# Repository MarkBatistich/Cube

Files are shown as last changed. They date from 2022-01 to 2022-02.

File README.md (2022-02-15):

# Cube

## Dynamic Model

To start, I drew a model of the sytem and defined some variables.

20220209_165314000_iOS

$\theta_w$ - angle of the wheel

$\theta_f$ - angle of the frame

$T$ - motor torque

$C_w$ - motor friction torque coefficient

$C_f$ - frame friction torque coefficient

$F_w$ - force of gravity on the wheel

$F_f$ - force of gravity on the frame

$I_c^o$ - moment of inertia of the cube about the origin

$I_w$ - moment of inertia of the wheel about its center of mass

$M_c^o$ - moment on the cube about the origin

$M_w$ - moment of the wheel about its center of mass

$m_w$ - mass of the wheel

$m_f$ - mass of the frame

$m_c$ - mass of the cube

$l_w$ - distance between the wheel's center of mass and the origin

$l_f$ - distance between the frame's center of mass and the origin

$l_c$ - distance between the cube's center of mass and the origin

I also defined the intertial axis such that +x is parellel to an unsloped surface and parallel to the cube face, +y is normal to an unsloped surface in the opposite direction as the force of gravity, and +z is in the direction of counterclockwise (CCW) wheel rotation. The origin O is placed at the corner of the cube touching the surface.

The equations of motion are constructed from the moments.

$M_c^o = I_c^o\ddot{\theta}_f = m_cl_cgsin(\theta_f) - (T - C_w\dot{\theta_w})-C_f\dot{\theta}_f$

$M_w = I_w(\ddot{\theta}_f+\ddot{\theta}_w) = T-C_w\dot{\theta_w}$

The cube moment of inertia about the origin can be found from the parallel axis theorem.

$I_c^o = I_f^o + I_w^o = I_f+m_fl_f^2 + I_w+m_wl_w^2$

The moment equations are solved for angular acceleration

$\ddot{\theta}_f = \frac{m_cl_cgsin(\theta_f)-T+C_w\dot{\theta_w}-C_f\dot{\theta}_f}{I_c^o}$

$\ddot{\theta}_w = \frac{T- C_w\dot{\theta_w}}{I_w} - \ddot{\theta}f$

From these equations, a state space model is made:

$x_1=\theta_f, x_2=\dot{\theta}_f,x_3=\dot{\theta}_w$

$\dot{x}_1 = x_2$

$\dot{x}_2 = \frac{m_cl_cgsin(\theta_f)-T+C_w\dot{\theta_w}-C_f\dot{\theta}_f}{I_c^o}$

$\dot{x}_3 = \frac{T- C_w\dot{\theta_w}}{I_w} - \frac{m_cl_cgsin(\theta_f)-T+C_w\dot{\theta_w}-C_f\dot{\theta}_f}{I_c^o}$

The small angle approximation is applied: $\sin(\dot{\theta}_f)=\dot{\theta}_f$

The torque is related to the pwm input $u$ by the equation:

$T = K_tu$

where $K_t$ is the motor torque constant.

The state space equations are put into matrix form:

$\begin{bmatrix}
\dot{x}_1 \\
\dot{x}_2 \\
\dot{x}_3 
\end{bmatrix} = 
\begin{bmatrix}
0 & 1 & 0\\
\frac{m_cl_cg}{I_c^o} & -\frac{C_f}{I_c^o} & \frac{C_w}{I_c^o}\\
-\frac{m_cl_cg}{I_c^o} & \frac{C_f}{I_c^o} & -\frac{C_w}{I_w}-\frac{C_w}{I_c^o}
\end{bmatrix}
\begin{bmatrix}
x_1 \\
x_2 \\
x_3 
\end{bmatrix} + 
\begin{bmatrix}
0 \\
-\frac{K_t}{I_c^o} \\
\frac{K_t}{I_w}-\frac{K_t}{I_c^o}
\end{bmatrix} u $

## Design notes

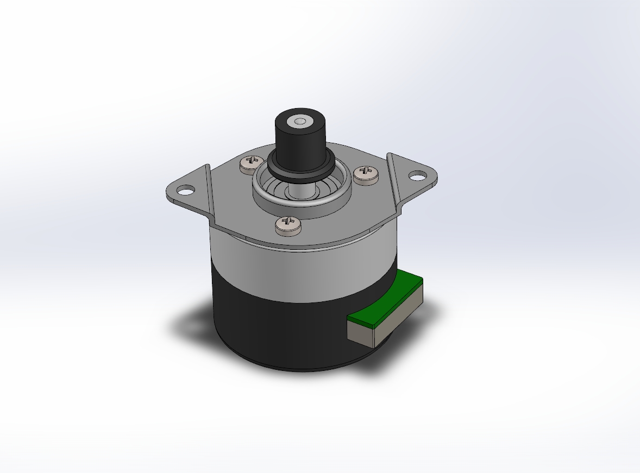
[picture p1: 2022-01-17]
CAD/c.jpg

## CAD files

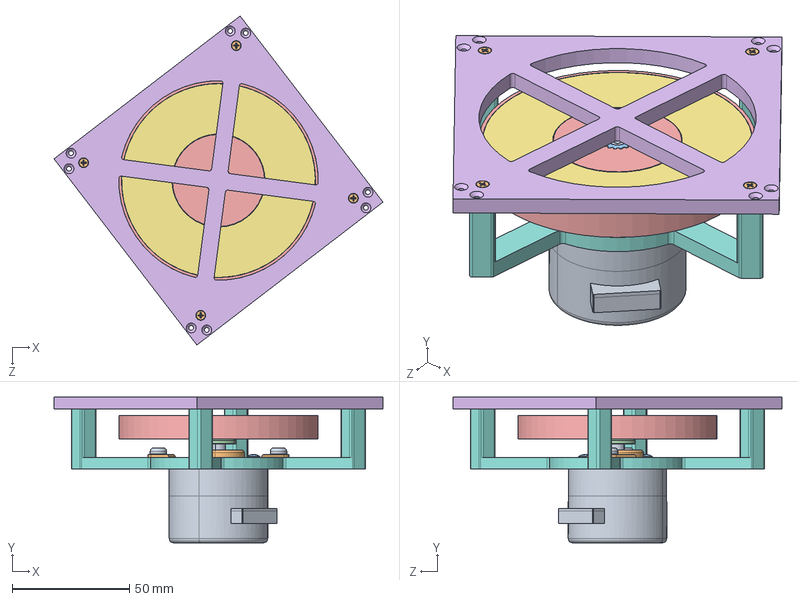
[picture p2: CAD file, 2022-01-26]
CAD/MotorAssembly.SLDASM
140.2 x 62.0 x 140.2 mm
motor.STEP
mount_plate.STEP
pan head cross recess screw_iso_ISO 7045 - M3 x 4 - Z - 4N.STEP x 3
pulley_nidec.STEP
Wheel
WheelCover
92141A041_18-8 Stainless Steel Washer x 2
MotorHolder2
99461A963_Phillips Rounded Head Thread-Forming Screws x 2
90485A416_Stainless Steel Flat Head Thread-Forming Screws for Plastic x 4
Geare

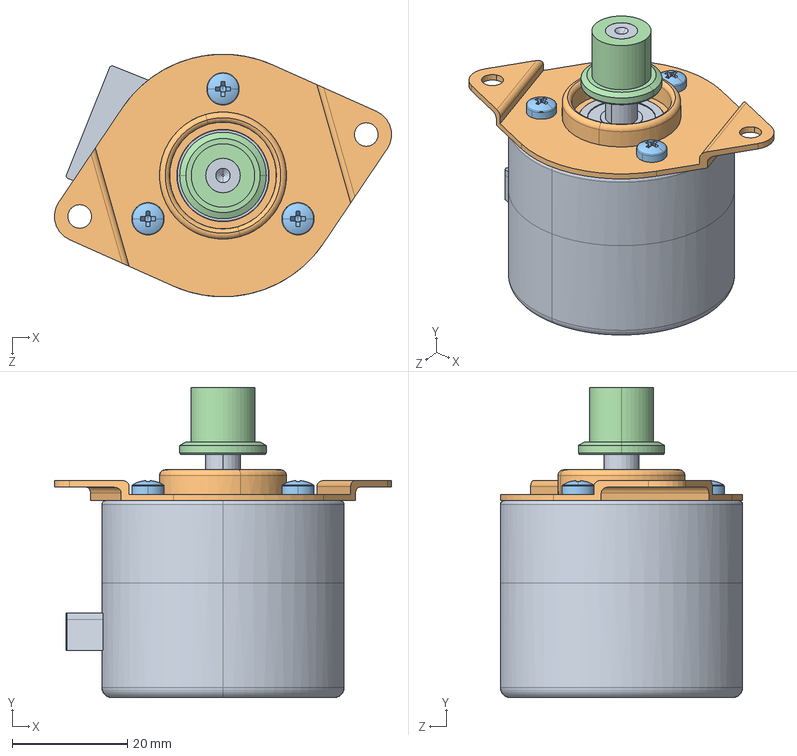
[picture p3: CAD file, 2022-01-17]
CAD/Motor.SLDASM
58.4 x 53.8 x 42.0 mm
motor.STEP
mount_plate.STEP
pan head cross recess screw_iso_ISO 7045 - M3 x 4 - Z - 4N.STEP x 3
pulley_nidec.STEP

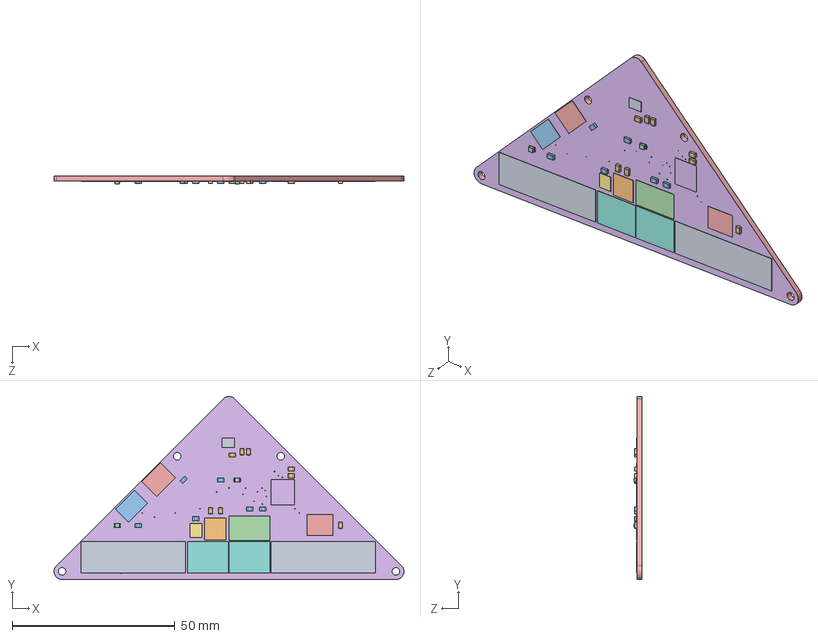
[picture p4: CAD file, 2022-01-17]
CAD/pcb v8.step.SLDASM
107.5 x 56.3 x 2.50 mm
PQFN50P300X250X97-14N.step
AP220533YR13.step
CUS-12B.step
OS102011MS2QS1.step
PTS526SM15SMTR2LFS.step x 2
SOP65P640X120-20N.step
SOT95P285X140-3N.step
TB00250002BE.step x 2
TB00250006BE.step x 2
C0805.step x 8
R0805.step x 6
CHIP-LED0805.step x 2
Board.step
1-soldermask.step
16-soldermask.step

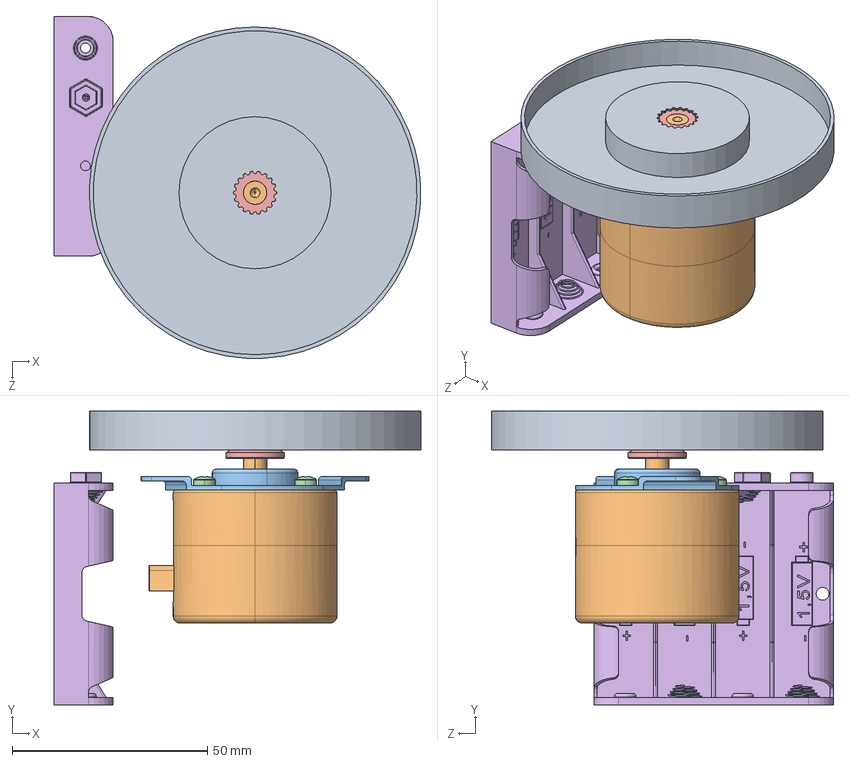
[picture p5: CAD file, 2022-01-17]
CAD/Assem.SLDASM
94.0 x 75.3 x 87.7 mm
Wheel
motor.STEP
mount_plate.STEP
pan head cross recess screw_iso_ISO 7045 - M3 x 4 - Z - 4N.STEP x 3
pulley_nidec.STEP
Battery2

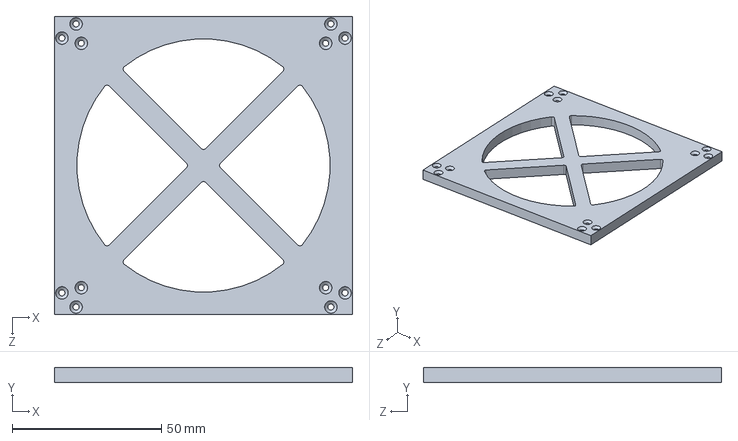
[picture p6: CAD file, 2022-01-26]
CAD/WheelCover.SLDPRT
100.0 x 5.00 x 100.0 mm

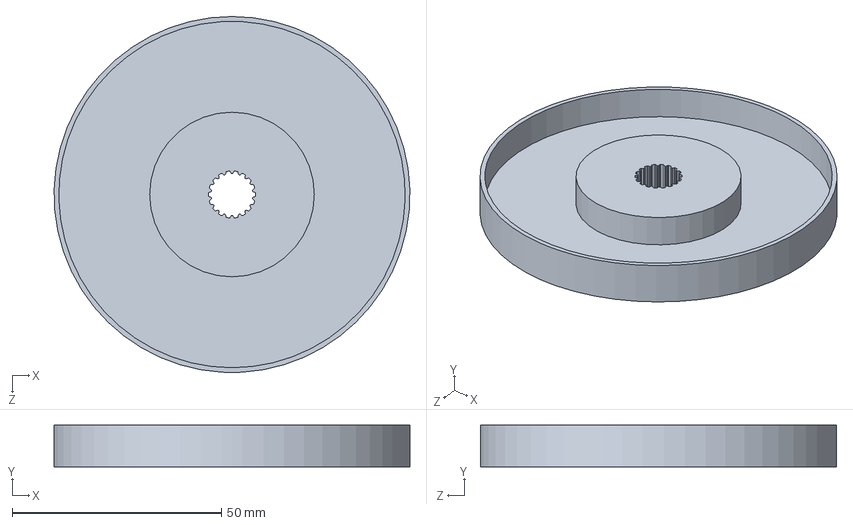
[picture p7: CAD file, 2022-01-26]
CAD/Wheel.SLDPRT
85.0 x 10.0 x 85.0 mm

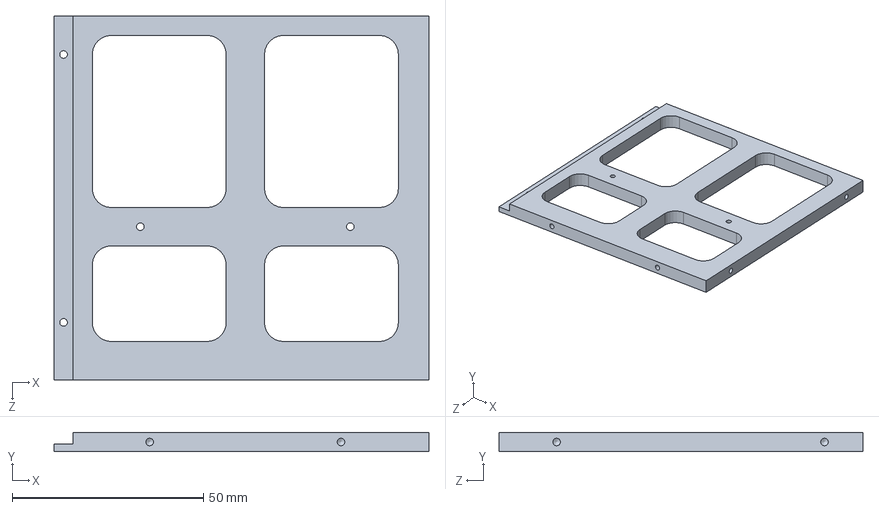
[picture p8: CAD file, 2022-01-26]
CAD/Wall.SLDPRT
98.0 x 5.00 x 95.0 mm

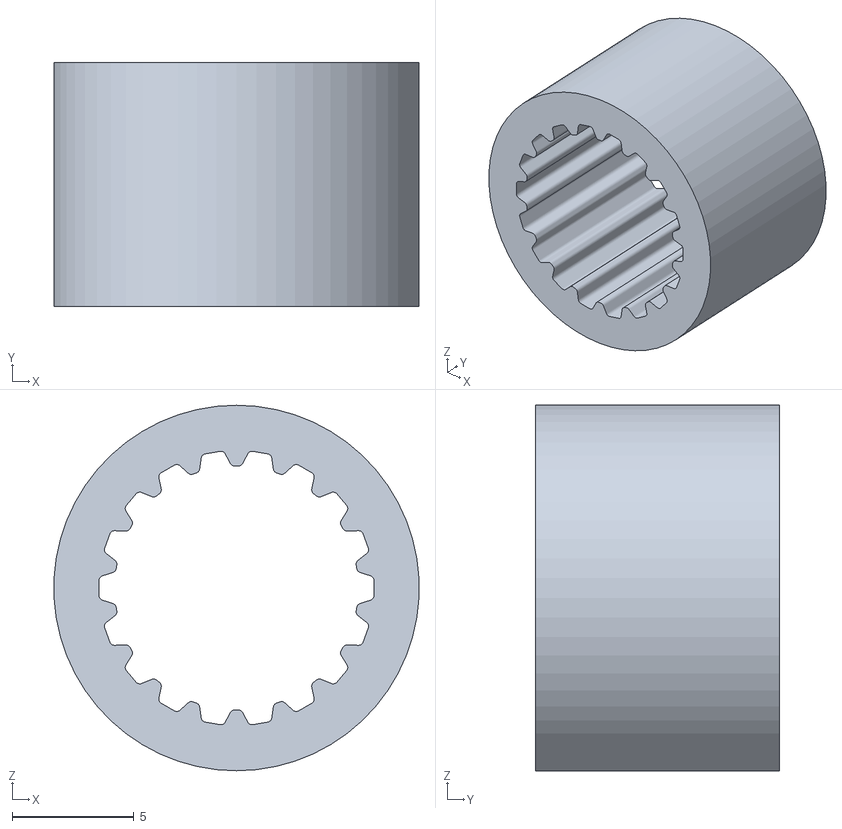
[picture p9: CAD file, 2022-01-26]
CAD/GearTest.STL
15.0 x 10.0 x 15.0

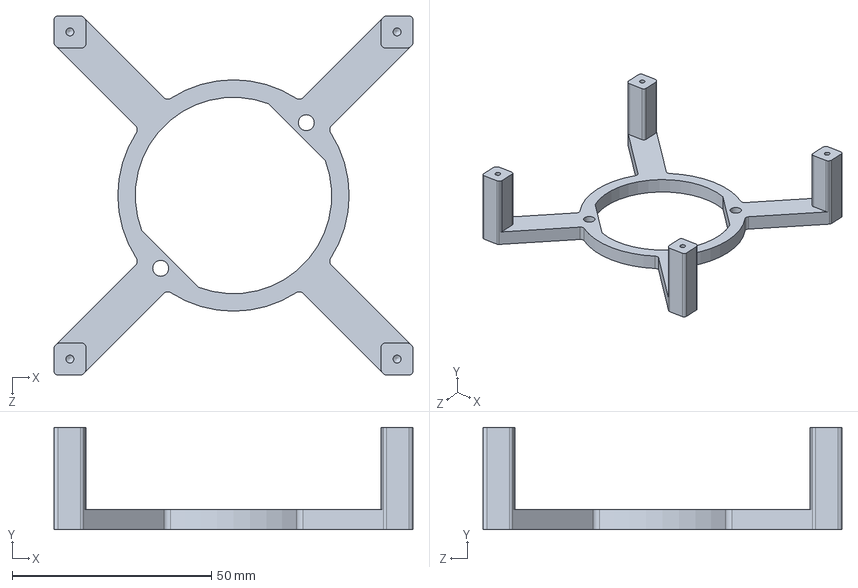
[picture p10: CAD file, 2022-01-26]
CAD/MotorHolder2.SLDPRT
90.0 x 25.6 x 90.0 mm

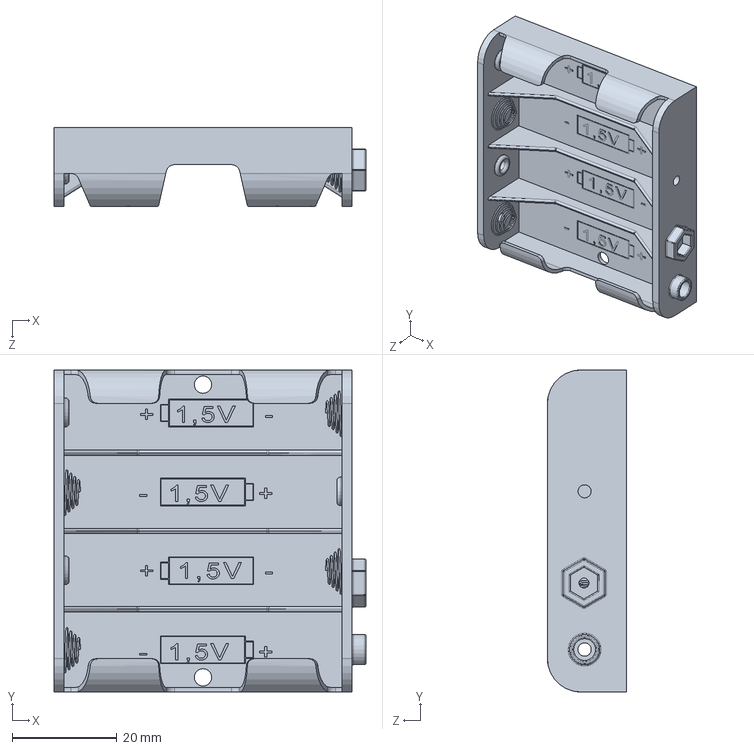
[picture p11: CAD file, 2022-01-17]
CAD/Battery2.SLDPRT
59.6 x 61.5 x 15.1 mm

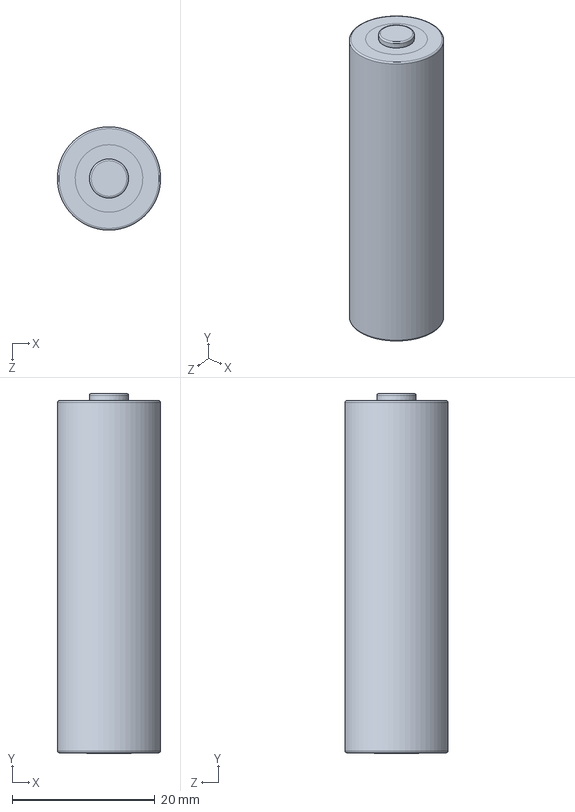
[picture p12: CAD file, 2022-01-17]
CAD/AA Battery.SLDPRT
14.5 x 50.5 x 14.5 mm

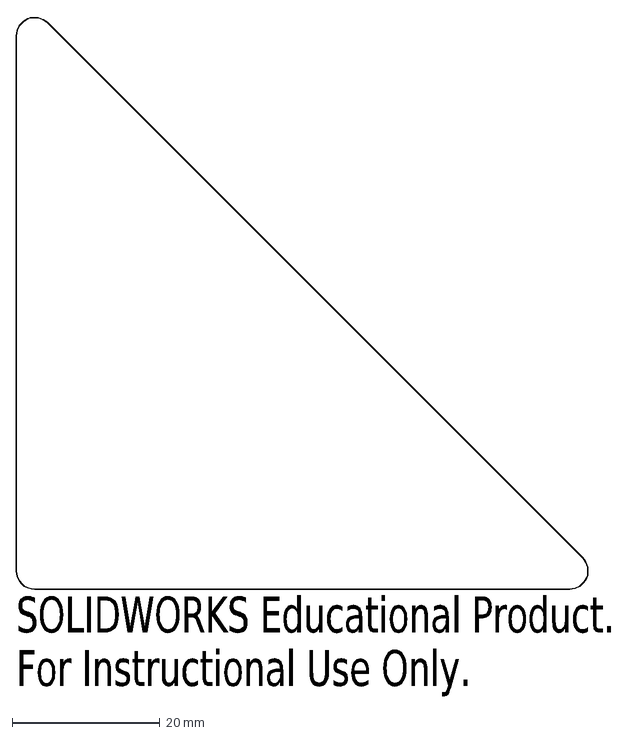
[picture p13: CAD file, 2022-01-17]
CAD/PCBshape1.DXF
SOLIDWORKS Educational Product.
For Instructional Use Only.

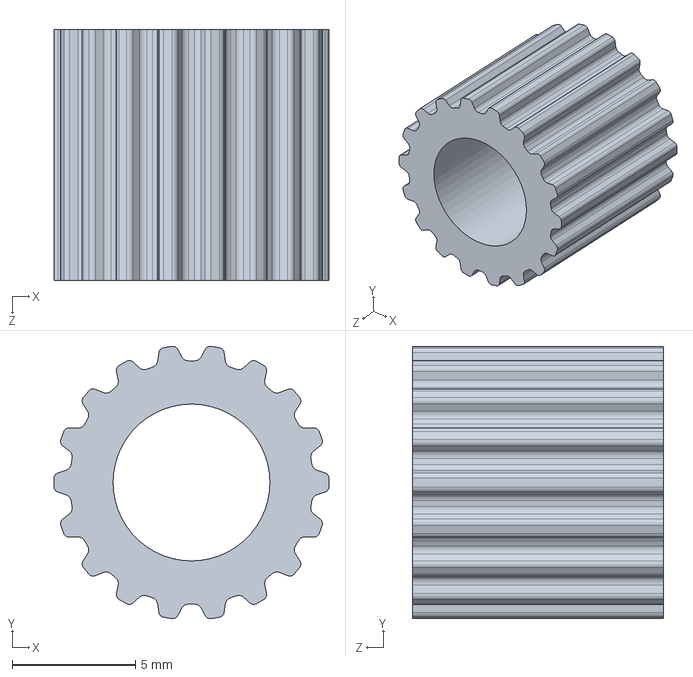
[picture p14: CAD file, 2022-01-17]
CAD/Geare.SLDPRT
11.1 x 11.0 x 10.2 mm

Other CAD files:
CAD/Packages.step.SLDASM
CAD/CHIP-LED0805.step.SLDPRT
CAD/Assem1.STEP
CAD/PTS526SM15SMTR2LFS.step.SLDPRT
CAD/pcb v8-2.step
CAD/1-copper.step.SLDPRT
CAD/1-soldermask.step.SLDPRT
CAD/16-soldermask.step.SLDPRT
CAD/7712K14_Battery Holder.SLDPRT
CAD/90107A042_316 Stainless Steel Washer.SLDPRT
CAD/90485A416_Stainless Steel Flat Head Thread-Forming Screws for Plastic.SLDPRT
CAD/92141A041_18-8 Stainless Steel Washer.SLDPRT
CAD/99461A922_Phillips Rounded Head Thread-Forming Screws.SLDPRT
CAD/99461A963_Phillips Rounded Head Thread-Forming Screws.SLDPRT
CAD/AP220533YR13.step.SLDPRT
CAD/Assem1.IGS
CAD/Assem1.STL
CAD/Assem1.x_b
CAD/Battery.SLDPRT
CAD/Board.step.SLDPRT
CAD/BoardShapeTest.SLDPRT
CAD/C0805.step.SLDPRT
CAD/CUS-12B.step.SLDPRT
CAD/MotorHolder.SLDPRT
CAD/MotorHolder2.STL
CAD/OS102011MS2QS1.step.SLDPRT
CAD/PQFN50P300X250X97-14N.step.SLDPRT
CAD/R0805.step.SLDPRT
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

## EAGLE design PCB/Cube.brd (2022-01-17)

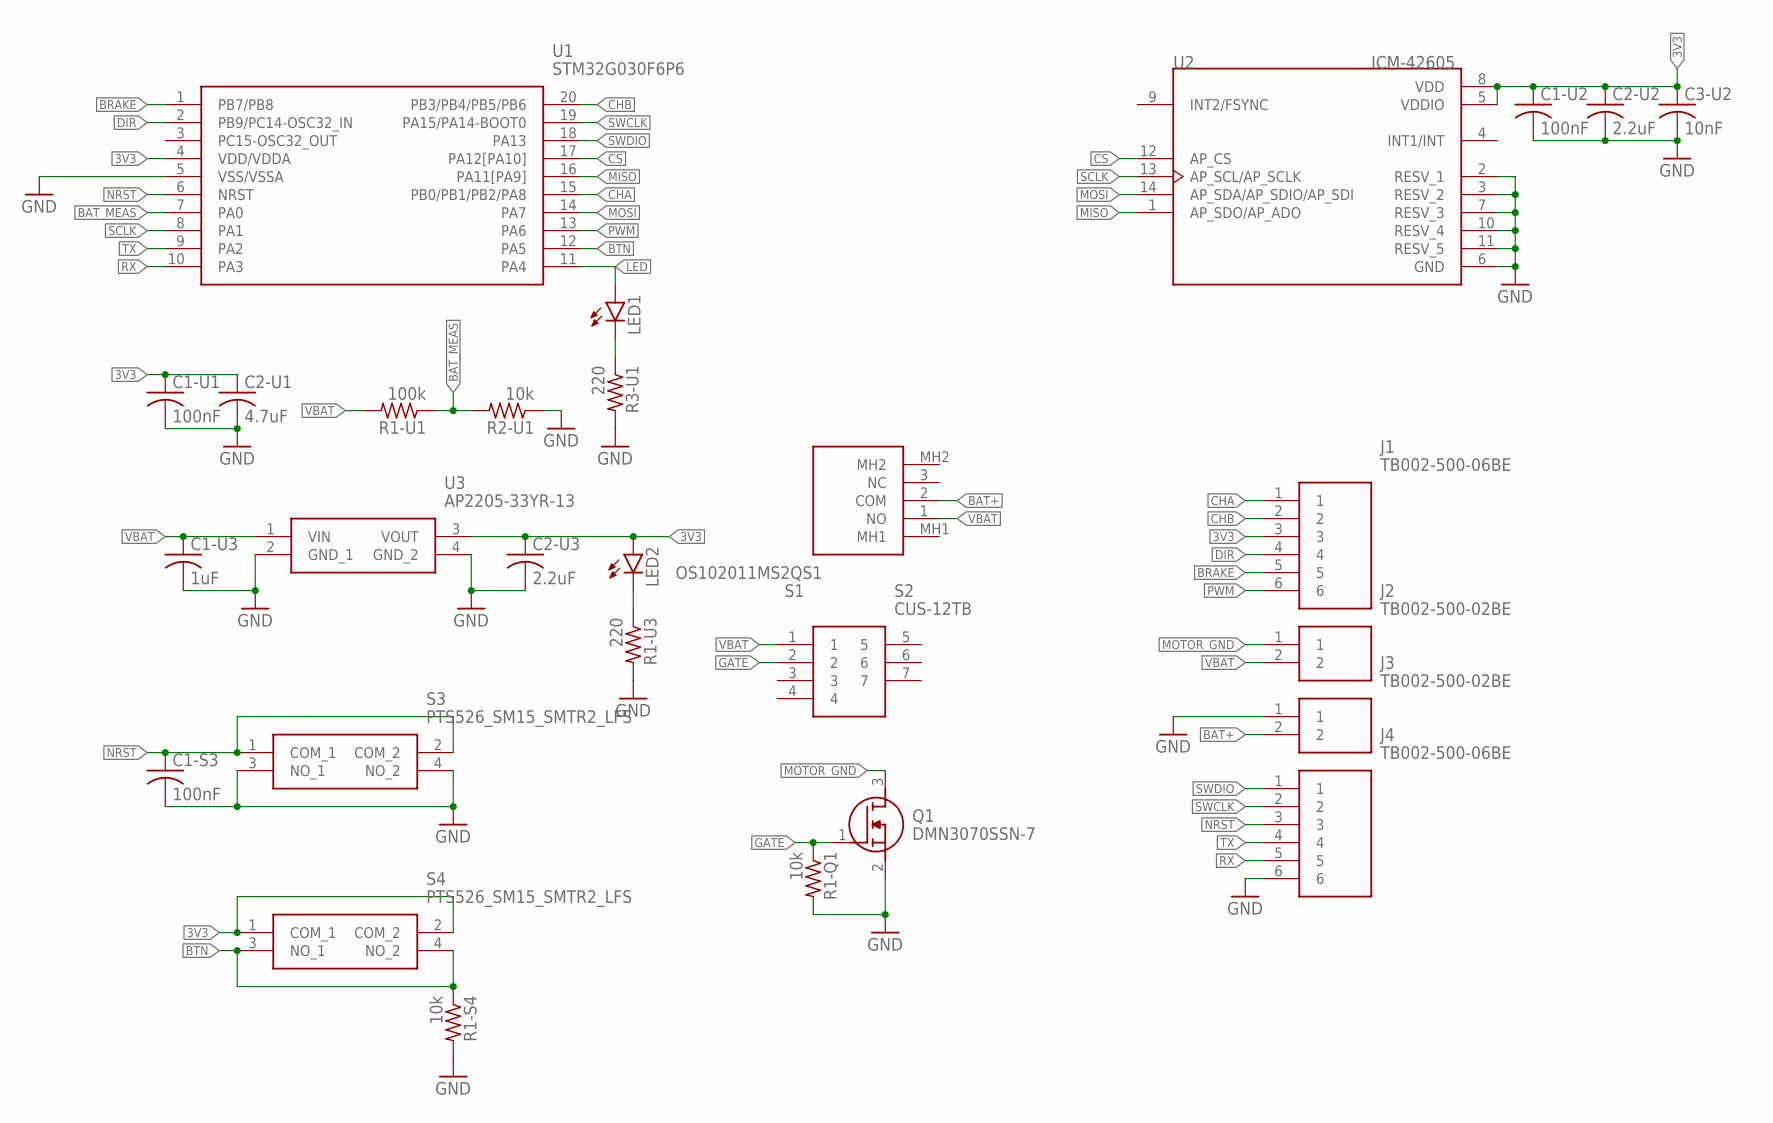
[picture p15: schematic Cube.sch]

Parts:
C1-S3, C1-U1, C1-U2: 100nF; C0805
C1-U3: 1uF; C0805
C2-U1: 4.7uF; C0805
C2-U2, C2-U3: 2.2uF; C0805
C3-U2: 10nF; C0805
J1, J4: TB002-500-06BE; TB00250006BE
J2, J3: TB002-500-02BE; TB00250002BE
LED1, LED2: LEDCHIP-LED0805; CHIP-LED0805
Q1: DMN3070SSN-7; SOT95P285X140-3N
R1-Q1, R1-S4, R2-U1: 10k; R0805
R1-U1: 100k; R0805
R1-U3, R3-U1: 220; R0805
S1: OS102011MS2QS1
S2: CUS-12TB; CUS-12B
S3, S4: PTS526_SM15_SMTR2_LFS; PTS526SM15SMTR2LFS
U1: STM32G030F6P6; SOP65P640X120-20N
U2: ICM-42605; PQFN50P300X250X97-14N
U3: AP2205-33YR-13; AP220533YR13

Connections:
3V3: C1-U1.1, C1-U2.1, C2-U1.1, C2-U2.1, C2-U3.1, C3-U2.1, J1.3, LED2.A, S4.1 (COM_1), S4.2 (COM_2), U1.4 (VDD/VDDA), U2.5 (VDDIO), U2.8 (VDD), U3.3 (VOUT)
BAT+: J3.2, S1.2 (COM)
BAT_MEAS: R1-U1.1, R2-U1.2, U1.7 (PA0)
BRAKE: J1.5, U1.1 (PB7/PB8)
BTN: R1-S4.1, S4.3 (NO_1), S4.4 (NO_2), U1.12 (PA5)
CHA: J1.1, U1.15 (PB0/PB1/PB2/PA8)
CHB: J1.2, U1.20 (PB3/PB4/PB5/PB6)
CS: U1.17 (PA12[PA10]), U2.12 (AP_CS)
DIR: J1.4, U1.2 (PB9/PC14-OSC32_IN)
GATE: Q1.1 (G), R1-Q1.1, S2.2
GND: C1-S3.2, C1-U1.2, C1-U2.2, C1-U3.2, C2-U1.2, C2-U2.2, C2-U3.2, C3-U2.2, J3.1, J4.6, Q1.2 (S), R1-Q1.2, R1-S4.2, R1-U3.2, R2-U1.1, R3-U1.2, S3.3 (NO_1), S3.4 (NO_2), U1.5 (VSS/VSSA), U2.2 (RESV_1), U2.3 (RESV_2), U2.6 (GND), U2.7 (RESV_3), U2.10 (RESV_4), U2.11 (RESV_5), U3.2 (GND_1), U3.4 (GND_2)
LED: LED1.A, U1.11 (PA4)
LED1-R: LED1.C, R3-U1.1
LED2-R: LED2.C, R1-U3.1
MISO: U1.16 (PA11[PA9]), U2.1 (AP_SDO/AP_ADO)
MOSI: U1.14 (PA7), U2.14 (AP_SDA/AP_SDIO/AP_SDI)
MOTOR_GND: J2.1, Q1.3 (D)
NRST: C1-S3.1, J4.3, S3.1 (COM_1), S3.2 (COM_2), U1.6 (NRST)
PWM: J1.6, U1.13 (PA6)
RX: J4.5, U1.10 (PA3)
SCLK: U1.8 (PA1), U2.13 (AP_SCL/AP_SCLK)
SWCLK: J4.2, U1.19 (PA15/PA14-BOOT0)
SWDIO: J4.1, U1.18 (PA13)
TX: J4.4, U1.9 (PA2)
VBAT: C1-U3.1, J2.2, R1-U1.2, S1.1 (NO), S2.1, U3.1 (VIN)

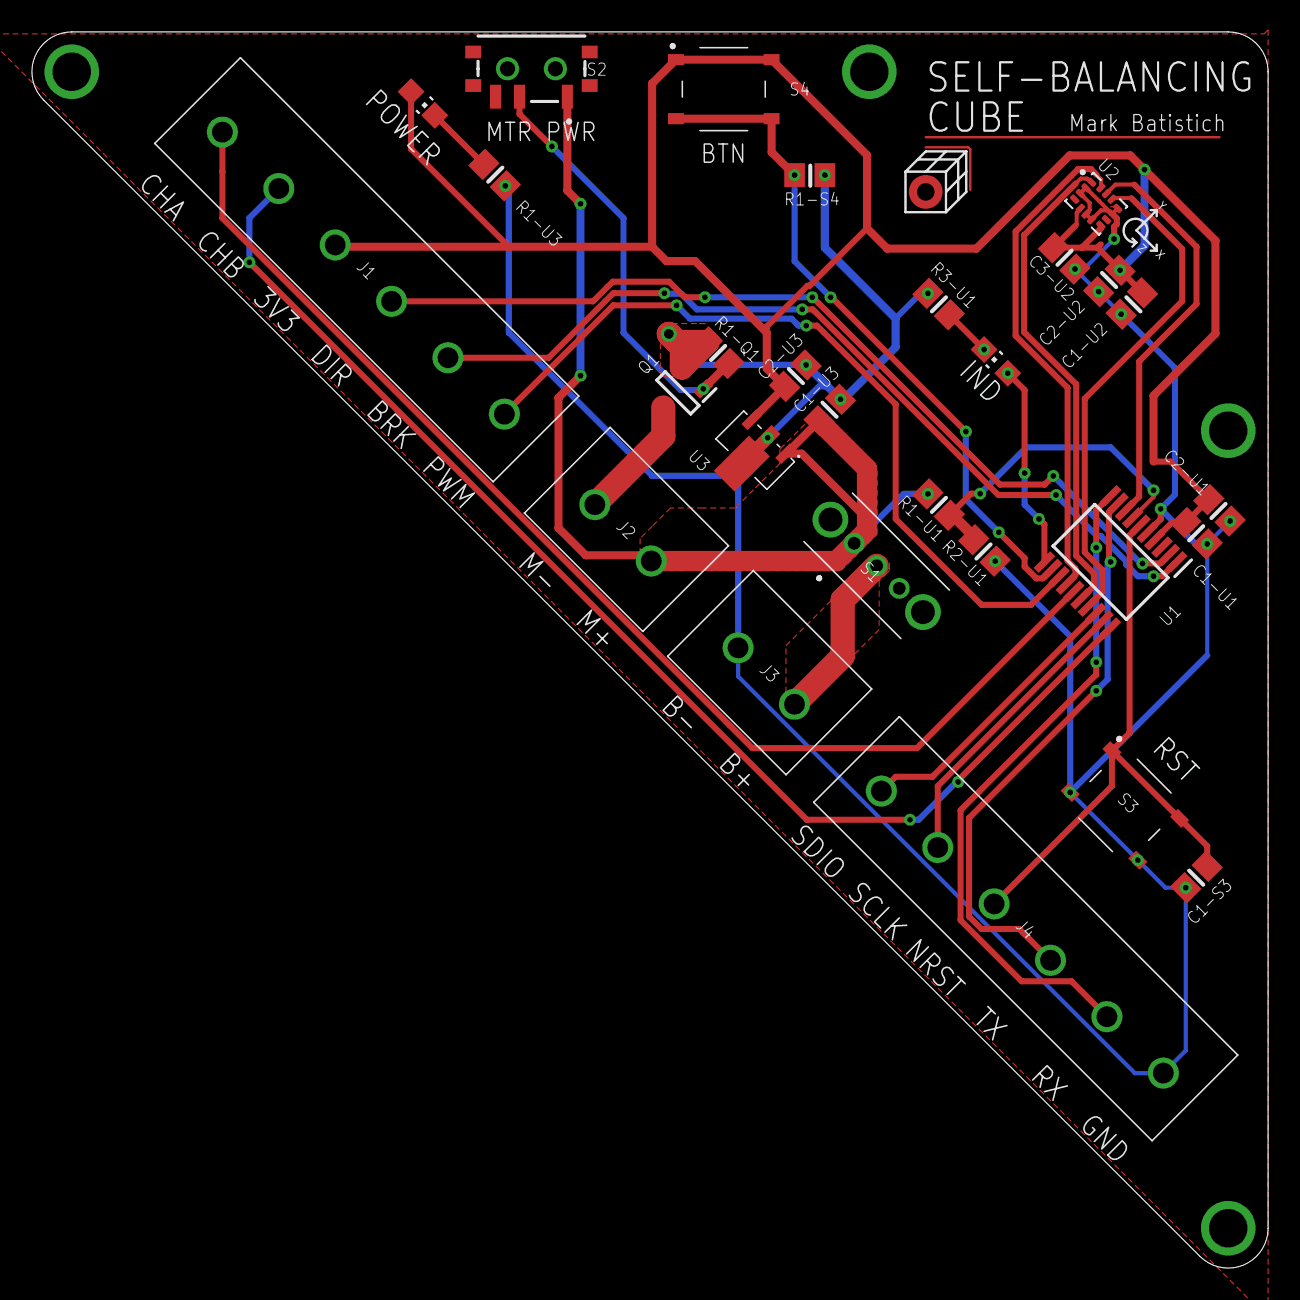
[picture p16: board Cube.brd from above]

Board: 2 copper layers, 77.5 x 77.5 mm, 28 parts (0 on the bottom side), 25 nets.

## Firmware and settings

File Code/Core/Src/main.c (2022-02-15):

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
/* Includes ------------------------------------------------------------------*/
#include "main.h"

/* USER CODE BEGIN Includes */
#include <stdio.h>
#include "fixmath.h"
//#include <math.h>
/* USER CODE END Includes */

ADC_HandleTypeDef hadc1;

SPI_HandleTypeDef hspi1;

TIM_HandleTypeDef htim1;
TIM_HandleTypeDef htim3;

UART_HandleTypeDef huart2;

void SystemClock_Config(void);
static void MX_GPIO_Init(void);
static void MX_TIM1_Init(void);
static void MX_TIM3_Init(void);
static void MX_USART2_UART_Init(void);
static void MX_ADC1_Init(void);
static void MX_SPI1_Init(void);
/* USER CODE BEGIN 0 */
int _write(int file, char *ptr, int len)
{
	HAL_UART_Transmit(&huart2, (uint8_t*)ptr, len, HAL_MAX_DELAY);
	return len;
}

void resetICM()
{
	uint8_t tx[2] = {W | DEVICE_CONFIG, 0x01};
	HAL_GPIO_WritePin (CS_GPIO_Port, CS_Pin, GPIO_PIN_RESET);
	HAL_SPI_Transmit(&hspi1, tx, 2, 1000);
	HAL_GPIO_WritePin (CS_GPIO_Port, CS_Pin, GPIO_PIN_SET);
	HAL_Delay(1);
}

void spiSet(uint8_t addr, uint8_t val)
{
	uint8_t tx[2] = {0};
	tx[0] = W | addr;
	tx[1] = val;
	HAL_GPIO_WritePin (CS_GPIO_Port, CS_Pin, GPIO_PIN_RESET);
	HAL_SPI_Transmit(&hspi1, tx, 2, SPI_WAIT);
	HAL_GPIO_WritePin (CS_GPIO_Port, CS_Pin, GPIO_PIN_SET);
}

void spiGet(uint8_t addr, uint8_t* rx, uint8_t num)
{
	uint8_t tx = R | addr;
	HAL_GPIO_WritePin (CS_GPIO_Port, CS_Pin, GPIO_PIN_RESET);
	HAL_SPI_Transmit(&hspi1, &tx, 1, SPI_WAIT);
	HAL_SPI_Receive(&hspi1, rx, num, SPI_WAIT);
	HAL_GPIO_WritePin (CS_GPIO_Port, CS_Pin, GPIO_PIN_SET);
}

void printf16(fix16_t num, int decimals){
	decimals = decimals > 5 ? 5 : decimals;
	char str[14] = {'0'};
	fix16_to_str(num, str, decimals);
	printf("%s", str);
}

void pn(){
	printf("\r\n");
}

void ps(){
	printf(" ");
}

void pc(){
	printf(", ");
}

void brakeOn() {
	HAL_GPIO_WritePin(BRAKE_GPIO_Port, BRAKE_Pin, GPIO_PIN_RESET);
	return;
}

void brakeOff() {
	HAL_GPIO_WritePin(BRAKE_GPIO_Port, BRAKE_Pin, GPIO_PIN_SET);
	return;
}

void waitUntilStop(){
	TIM3->CCR1 = 100;
	brakeOn();
	int val1 = 0;
	int val2 = 1;
	while (val1 != val2){
		val1 = TIM1->CNT;
		HAL_Delay (10);
		val2 = TIM1->CNT;
	}
	brakeOff();
}

fix16_t getBatteryVoltage() {
	HAL_ADC_Start(&hadc1);
	uint32_t raw;
	fix16_t voltage;
	HAL_ADC_PollForConversion(&hadc1, 1000);
	raw = HAL_ADC_GetValue(&hadc1);
	voltage = fix16_mul(fix16_from_int(raw), fix16_from_float(3.3/4095*0.9647)); // Vdd / 2^16 * fudgeFactor
	voltage = fix16_mul(voltage, fix16_from_float(11.07)); // resistor ratio
	voltage = fix16_sub(voltage, fix16_from_float(0.1)); // more fudge factor
	HAL_ADC_Stop(&hadc1);
	return voltage;
}

fix16_t rad2deg(fix16_t num){
	num = fix16_mul(num, fix16_from_int(180));
	num = fix16_div(num, fix16_pi);
	return num;
}

//returns 1 if the number is negative, 0 if positive or 0
int32_t sign(int32_t num){
	return (num < 0);
}
/* USER CODE END 0 */

/**
  * @brief  The application entry point.
  * @retval int
  */
int main(void)
{
  /* MCU Configuration--------------------------------------------------------*/

  /* Reset of all peripherals, Initializes the Flash interface and the Systick. */
  HAL_Init();

  /* Configure the system clock */
  SystemClock_Config();

  /* Initialize all configured peripherals */
  MX_GPIO_Init();
  MX_TIM1_Init();
  MX_TIM3_Init();
  MX_USART2_UART_Init();
  MX_ADC1_Init();
  MX_SPI1_Init();
  /* USER CODE BEGIN 2 */

  //Start timers and ADC
  HAL_TIM_PWM_Start(&htim3, TIM_CHANNEL_1);
  HAL_TIM_Encoder_Start(&htim1, TIM_CHANNEL_ALL);

  uint8_t rx[6] = { 0 };
  resetICM();
  spiSet(ACCEL_CONFIG0, 0x06);
  spiSet(GYRO_CONFIG0, 0x06);
  spiSet(PWR_MGMT0, 0x0F);
  HAL_Delay(45);

//  fix16_t P = fix16_from_float(32767.999985);
//  fix16_t Q = fix16_atan2(140351, 65536);
//  P = fix16_div(P,Q);
//  Q = fix16_mul(Q, fix16_from_int(2));
//  P = fix16_sqrt(P);

  printf("start\r\n");
  pn();


  //variable definitions
  int16_t pos1 = 0, pos2 = 0, diff = 0;
  fix16_t angle = 0, prevAngle = 0, gyrAngle = 0, accAngle = 0;
  uint32_t start = 0, end = 0;
  uint8_t dir = 1;
  uint32_t pulse = TIM3->CCR1;
  int32_t control = 0, controlSignal = 0;
  int16_t a_i[3] = {0};
  fix16_t a_f[3] = {0};
  int16_t g_i[3] = {0};
  fix16_t g_f[3] = {0};
  fix16_t error = 0, errorInt = 0, errorDiff = 0;
  fix16_t velocity = 0;
  fix16_t controlVelocity = 0;
  fix16_t velocityError = 0, velocityErrorInt = 0, velocityErrorDiff = 0;
  fix16_t prevVelocityError = 0;
  uint8_t firstRun = 1;
  fix16_t angleControl, velocityControl = 0;


  const uint32_t dt = 10;
  const fix16_t tau = fix16_from_int(1);
  const fix16_t alpha = fix16_div(tau, fix16_add(tau, fix16_div(fix16_from_int(dt), fix16_from_int(1000))));
  const fix16_t accFactor = fix16_div(fix16_from_int(16), fix16_from_int(32768));
  const fix16_t gyrFactor = fix16_div(fix16_from_int(2000), fix16_from_int(32768));
  const fix16_t Kp = fix16_from_float(80.00);
  const fix16_t Ki = fix16_from_float(3.000);
  const fix16_t Kd = fix16_from_float(200.00);
  const fix16_t Kp_s = fix16_from_float(10.00);
  const fix16_t Ki_s = fix16_from_float(0.00);
  const fix16_t Kd_s = fix16_from_float(0.00);

  HAL_GPIO_WritePin(DIR_GPIO_Port, DIR_Pin, GPIO_PIN_RESET);
  HAL_GPIO_WritePin(LED_GPIO_Port, LED_Pin, GPIO_PIN_RESET);
  HAL_GPIO_WritePin(DIR_GPIO_Port, DIR_Pin, GPIO_PIN_SET);
  waitUntilStop();
  TIM3->CCR1 = 100;

  spiGet(WHO_AM_I, rx, 1);
  printf("WHO_AM_I: %d\r\n", rx[0]);
  HAL_Delay(1000);
  /* USER CODE END 2 */

  /* Infinite loop */
  /* USER CODE BEGIN WHILE */
  while (1)
  {
    /* USER CODE END WHILE */

    /* USER CODE BEGIN 3 */
	  start = HAL_GetTick();

	  pos1 = pos2;
	  pos2 = TIM1 -> CNT;
	  diff = pos2 - pos1;
	  if (diff < 0) diff += 65536;

	  spiGet(ACCEL_DATA_X1, rx, 6);

	  a_i[0] = (rx[0] << 8) | rx[1];
	  a_i[1] = (rx[2] << 8) | rx[3];
	  a_i[2] = (rx[4] << 8) | rx[5];

	  a_f[0] = fix16_mul(fix16_from_int(a_i[0]), accFactor);
	  a_f[1] = fix16_mul(fix16_from_int(a_i[1]), accFactor);
	  a_f[2] = fix16_mul(fix16_from_int(a_i[2]), accFactor);

	  spiGet(GYRO_DATA_X1, rx, 6);

	  g_i[0] = (rx[0] << 8) | rx[1];
	  g_i[1] = (rx[2] << 8) | rx[3];
	  g_i[2] = (rx[4] << 8) | rx[5];

	  g_f[0] = fix16_mul(fix16_from_int(g_i[0]), gyrFactor);
	  g_f[1] = fix16_mul(fix16_from_int(g_i[1]), gyrFactor);
	  g_f[2] = fix16_mul(fix16_from_int(g_i[2]), gyrFactor);

	  prevAngle = angle;
	  accAngle = fix16_atan2(-a_f[0], -a_f[1]);
	  accAngle = rad2deg(accAngle);
	  accAngle = fix16_sub(accAngle, fix16_from_float(1.5));

	  if (firstRun){
		  gyrAngle = accAngle;
		  angle = accAngle;
	  }

	  gyrAngle = fix16_add(angle, fix16_mul(-g_f[2], fix16_div(fix16_from_int(dt), fix16_from_int(1000))));

	  angle = fix16_add(fix16_mul(alpha, gyrAngle), fix16_mul(fix16_sub(fix16_one, alpha), accAngle));


	  //HAL_GPIO_TogglePin (LED_GPIO_Port, LED_Pin);

	  error = angle;
	  errorDiff = fix16_sub(angle, prevAngle);
	  errorInt += error;
	  prevAngle = angle;

	  velocity = fix16_div(fix16_from_int(diff), fix16_from_int(200));
	  velocity = fix16_mul(velocity, fix16_from_int(1000/dt));

	  velocityError = velocity;
	  velocityErrorDiff = fix16_sub(velocityError, prevVelocityError);
	  velocityErrorInt += velocityError;
	  prevVelocityError = velocityError;



//	  error = angle;
//	  errorDiff = fix16_sub(angle, prevAngle);
//	  errorInt += error;
//	  control = fix16_to_int(fix16_add(fix16_add(fix16_mul(Kp, error), fix16_mul(Ki, errorInt)), fix16_mul(Kd, errorDiff)));
//
//	  control = MAX(MIN(control, 100), -100);
//	  //Ensure motor is stopped before switching directions
////	  if((sign(control) != sign(diff)) && diff != 0) {
////		  waitUntilStop();
////		  dir = !sign(control);
////		  HAL_GPIO_WritePin(DIR_GPIO_Port, DIR_Pin, dir);
////	  }
//
//	  controlSpeed = fix16_mul(fix16_from_int(control), fix16_from_float(36 / 100.0));
//	  prevvelocityError = velocityError;
//	  velocityError = fix16_sub(controlSpeed, speed);
//	  velocityErrorDiff = fix16_sub(velocityError, prevvelocityError);
//	  velocityErrorInt += velocityError;
//	  controlSignal = fix16_add(fix16_add(fix16_mul(Kp_s, velocityError), fix16_mul(Ki_s, velocityErrorInt)), fix16_mul(Kd_s, velocityErrorDiff));
//
//	  controlSignal = fix16_mul(controlSignal, fix16_from_float(100 / 36.0));
//	  controlSignal = MAX(MIN(controlSignal, fix16_from_int(100)), fix16_from_int(-100));
//	  controlSignal = fix16_to_int(controlSignal);

	  angleControl = fix16_add(fix16_add(fix16_mul(Kp, error), fix16_mul(Ki, errorInt)), fix16_mul(Kd, errorDiff));
	  velocityControl = fix16_add(fix16_add(fix16_mul(Kp_s, velocityError), fix16_mul(Ki_s, velocityErrorInt)), fix16_mul(Kd_s, velocityErrorDiff));

	  control = fix16_add(angleControl, -velocityControl);

	  control = MAX(MIN(control, fix16_from_int(100)), fix16_from_int(-100));
	  controlSignal = fix16_to_int(control);

	  controlVelocity = fix16_mul(control, fix16_from_float(100 / 36.0));

	  if (fix16_sub(fix16_abs(controlVelocity), fix16_abs(velocity)) > 0 && ((sign(controlSignal) == sign(velocity)) || (fix16_abs(velocity) < fix16_from_int(10)))) {
		  pulse = 100 - (controlSignal * (1-2*(controlSignal<0)));
		  brakeOff();
	  } else {
		  pulse = 100;
		  brakeOn();
	  }

	  if (fix16_abs(velocity) < fix16_from_int(10)) {
		  dir = !sign(controlSignal);
		  HAL_GPIO_WritePin(DIR_GPIO_Port, DIR_Pin, dir);
	  }

	  if (fix16_abs(angle) > fix16_from_int(25)) {
		  pulse = 100;
		  errorInt = 0;
	  }

	  TIM3->CCR1 = pulse;

//	  printf("%d %d %d ", control, pulse, controlSignal);
//	  printf16(speed,2);
//	  ps();
//	  printf16(controlSpeed, 2);
//	  pn();


	  //TIM3->CCR1 = 80;
	  printf("%d, ", HAL_GetTick());
	  printf16(angleControl, 2);
	  pc();
	  printf16(velocityControl, 2);
	  pc();
	  printf16(control, 2);
	  pc();
	  printf16(angle, 2);
	  pc();
	  printf("%d, ", pulse);
	  pn();

	  end = HAL_GetTick();
	  while (end-start < dt){
		  HAL_Delay(0);
		  end = HAL_GetTick();
	  }

	  firstRun = 0;
	  //printf("Tick Time: %d\n", end-start);
	  //pn();
  }
  /* USER CODE END 3 */
}

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


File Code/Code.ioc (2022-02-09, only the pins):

Mcu.UserName=STM32G030F6Px
PA0.GPIO_Label=BAT_MEAS
PA0.Signal=ADC1_IN0
PA1.Signal=SPI1_SCK
PA13.Signal=SYS_SWDIO
PA14-BOOT0.Signal=SYS_SWCLK
PA2.Signal=USART2_TX
PA3.Signal=USART2_RX
PA4.GPIO_Label=LED
PA4.Signal=GPIO_Output
PA5.GPIO_Label=BTN
PA5.Signal=GPIO_Input
PA6.Signal=S_TIM3_CH1
PA7.Signal=SPI1_MOSI
PA8.Signal=S_TIM1_CH1
PB3.Signal=S_TIM1_CH2
PB8.GPIO_Label=BRAKE
PB8.Signal=GPIO_Output
PB9.GPIO_Label=DIR
PB9.Signal=GPIO_Output

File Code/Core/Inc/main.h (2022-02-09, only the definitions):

#define BRAKE_Pin GPIO_PIN_8
#define BRAKE_GPIO_Port GPIOB
#define DIR_Pin GPIO_PIN_9
#define DIR_GPIO_Port GPIOB
#define BAT_MEAS_Pin GPIO_PIN_0
#define BAT_MEAS_GPIO_Port GPIOA
#define LED_Pin GPIO_PIN_4
#define LED_GPIO_Port GPIOA
#define BTN_Pin GPIO_PIN_5
#define BTN_GPIO_Port GPIOA
#define CS_Pin GPIO_PIN_12
#define CS_GPIO_Port GPIOA
#define ICM_ADDR 0x68 << 1
#define DEVICE_CONFIG 0x11
#define DRIVE_CONFIG 0x13
#define GYRO_DATA_X1 0x25
#define GYRO_DATA_X0 0x26
#define ACCEL_DATA_X1 0x1F
#define ACCEL_CONFIG0 0x50
#define PWR_MGMT0 0x4E
#define WHO_AM_I 0x75
#define GYRO_CONFIG0 0x4F
#define R (0x1) << 7
#define W (0x0) << 7
#define SPI_WAIT 1

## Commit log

2022-01-17 moved to github
    [1-copper.step.SLDPRT, 1-soldermask.step.SLDPRT, 16-soldermask.step.SLDPRT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]
2022-02-06 Updated code and models
    [Wheel.STL]
2022-02-09 Code updates
    [ADC.xlsx, MotorData.xlsx]
2022-02-10 Code and readme development. Nearly stable cube
    [MotorData.xlsx]
2022-02-15 stable code with long term balance
    [MotorData.xlsx]

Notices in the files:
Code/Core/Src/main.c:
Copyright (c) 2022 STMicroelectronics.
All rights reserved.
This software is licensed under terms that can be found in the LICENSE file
